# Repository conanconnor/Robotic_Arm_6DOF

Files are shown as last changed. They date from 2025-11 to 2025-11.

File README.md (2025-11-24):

# Robotic Arm 6-DOF

| **Christopher Abdul-Ahad** | **Conan Connor** |
|---|---|
| [GitHub](https://github.com/christopherabdulahad) · [LinkedIn](https://www.linkedin.com/in/christopherabdul-ahad/) | [GitHub](https://github.com/conanconnor) · [LinkedIn](https://www.linkedin.com/in/conanconnor/) |

A fully custom 6 degree of freedom robotic arm designed, built and programmed from scratch. This project was created as a personal engineering project to explore building a functional robotic system from the ground up.

https://github.com/user-attachments/assets/21fbbb61-f551-49d5-a1af-482c772e95da

<ins>**Goals**</ins>

The primary goal of this project was to design and build a fully functional custom 6-DOF pick-and-place robotic arm that could automate tasks similar to those found on assembly lines. As mechanical engineering students, we aimed to gain hands-on experience, implementing what we have learnt from theory - from initial CAD design to manufacturing, assembly and motion control programming. 

Our objectives included: 
- Understanding the complete robotics development process, from design to a fully operational product. 
- Designing a cost-effective, strong and reliable robotic arm, using 3D-printed components and commonly available hardware. 
- Developing motion control software in C++ using the Arduino IDE, achieving precise and predictable joint movements. 
- Creating a foundation for continuous improvement, allowing for future enhancements such as better actuators, sensors, and advanced control algorithms. 

This project was intended not only to produce a functional robotic manipulator but also to strengthen our capabilities in practical engineering design, prototyping and problem solving which are all key skills for any career in engineering. 

<ins>**Challenges**</ins>

Throughout the development process, we encountered several challenges, these include: 
- 3D printing tolerances: Very small holes and tight fit features designed in SolidWorks did not print accurately due to printer tolerances. 
- Support structure impact: Parts that required a lot of supports experienced surface imperfections or dimensional inaccuracies, affecting the assembly and motion smoothness. 
- Gravity and print orientation: Some components sagged during printing due to poor orientation or insufficient support. 
- Friction and mechanical losses: The gear system in the hand experienced higher friction than expected, reducing efficiency and motion smoothness. 
- Assembly complexity: Some components were difficult to fit together because accessibility was not fully considered during design. 

These challenges gave us valuable insight into Design for Manufacturing, specifically for additive manufacturing and low-cost robotics. 

<ins>**Solutions and Results**</ins>

To address these issues, we applied these solutions: 
- Drilling:  We used a hand drill to enlarge holes that printed undersized or not at all. 
- Sanding:  We sanded mating surfaces to improve fit and sliding motion. 
- Iterative redesign: Updated CAD models to correct structural or functional issues identified during testing. 

<ins>**Future Improvements**</ins>

If we were to continue developing this project or rebuild it from scratch we would add the following improvements: 
- Increase hole diameters in CAD to account for 3D-printing tolerances and avoid designing holes smaller than ~1 mm. 
- Optimise part geometry to reduce or eliminate the need for complex support structures. 
- Redesign print orientations to prevent sagging and ensure critical surfaces are printed cleanly. 
- Improve assembly by adding better access to screw holes 
- Refine the hand by redesigning gears to reduce friction and improve durability. 
- Upgrade control hardware in the future such as better servos, encoders or stepper motors for greater accuracy and load capacity. 




https://github.com/user-attachments/assets/dea5969e-bc63-4acd-a8a1-89a3208a30c9

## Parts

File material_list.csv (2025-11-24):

Catagory | Item | Quanitity
3D printed parts | All printed components | 24
Mechanical | M3 12mm countersunk screw | 18
Mechanical | M3 16mm countersunk screw | 7
Mechanical | M1 6mm screw | 6
Mechanical | M1.7 8mm screw | 16
Mechanical | M3 hexagon self-locking nylon nuts | 7
Electrical | Arduino UNO R3 | 1
Electrical | 5V 10A Power Supply | 1
Electrical | MG996R Servo Motor | 3
Electrical | SG90 Servo Motor | 3
Electrical | 30cm servo motor wire extender | 2
Electrical | 10cm servo motor wire extender | 1
Electrical | Male to male jumper wires | 4
Electrical | Female to male jumper wires | 15
Electrical | 16 AWG Wire | 1
Electrical | 10A Choc Block | 2

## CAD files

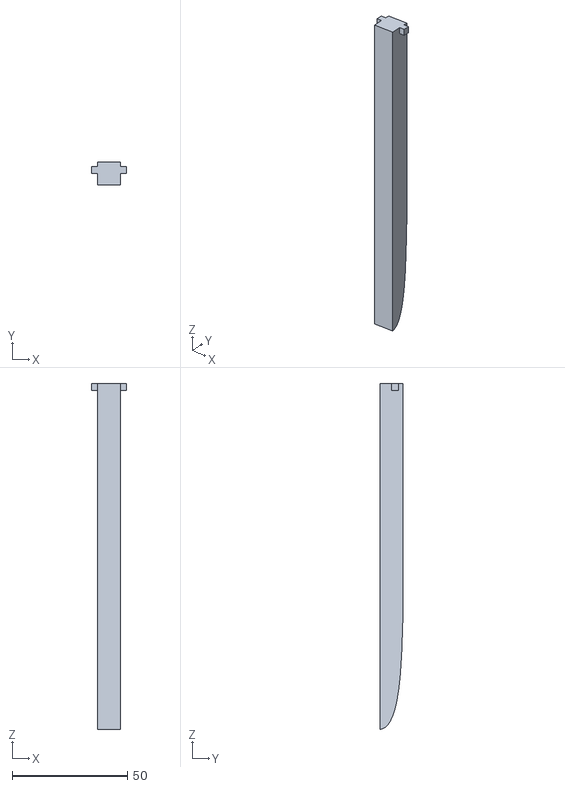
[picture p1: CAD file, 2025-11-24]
CAD/Leg_x6_BLUE.STL
15.0 x 10.0 x 150.0

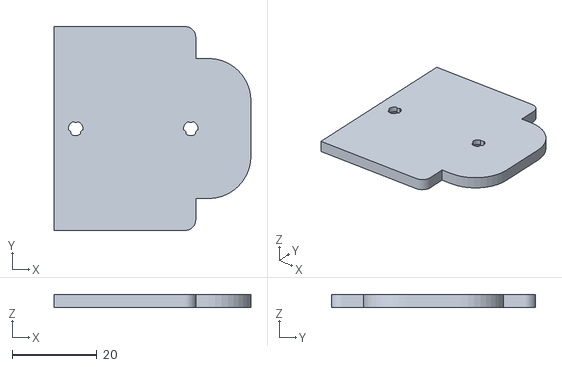
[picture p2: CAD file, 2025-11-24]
CAD/Hand_Base_Lid_BLUE.STL
46.4 x 48.0 x 3.00

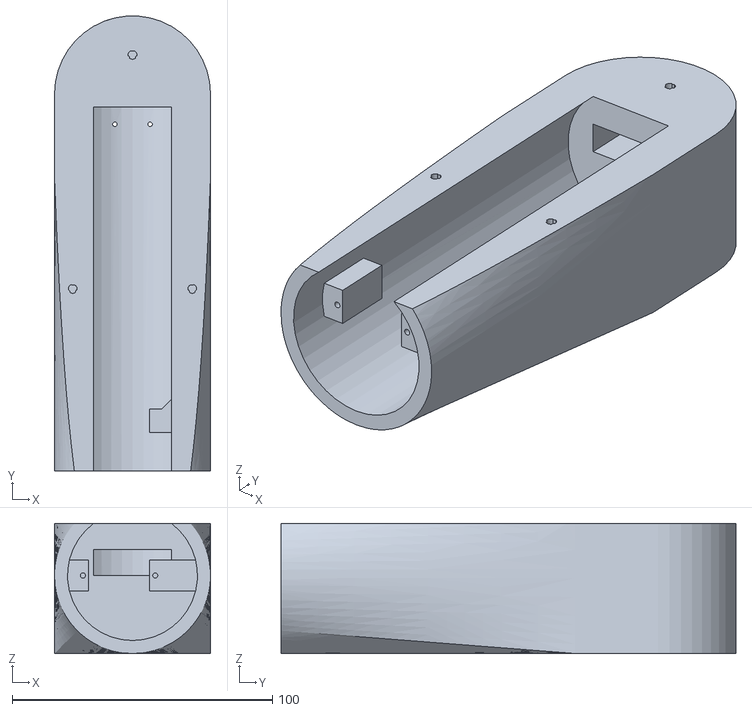
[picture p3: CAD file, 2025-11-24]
CAD/Forearm_BLUE.STL
60.0 x 174.9 x 50.0

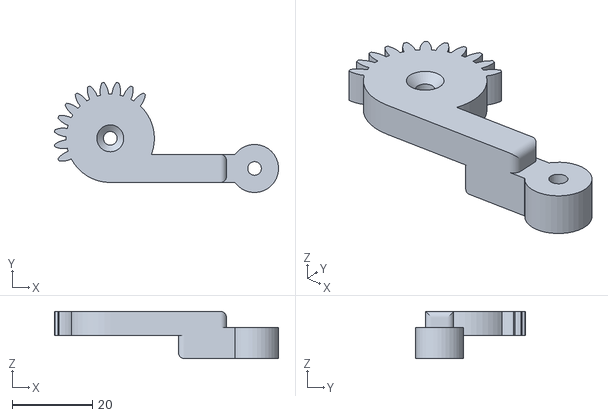
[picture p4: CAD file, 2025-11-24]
CAD/Hand_Mid_Otherside_WHITE.STL
55.9 x 27.4 x 11.8

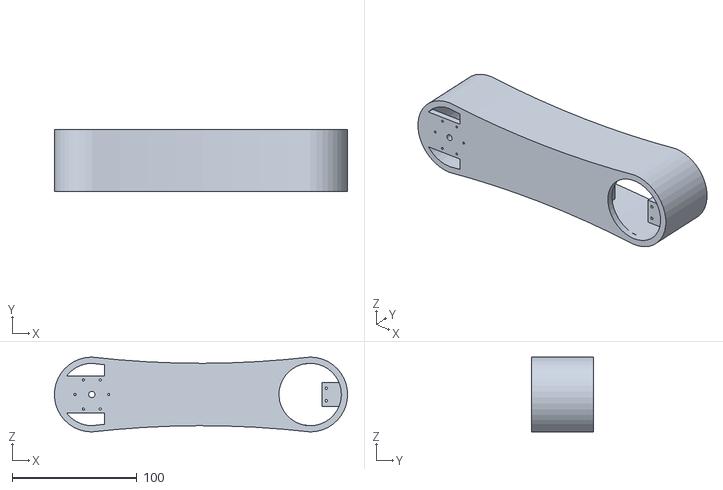
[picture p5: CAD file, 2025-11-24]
CAD/Upperarm_WHITE.STL
234.8 x 50.0 x 60.0

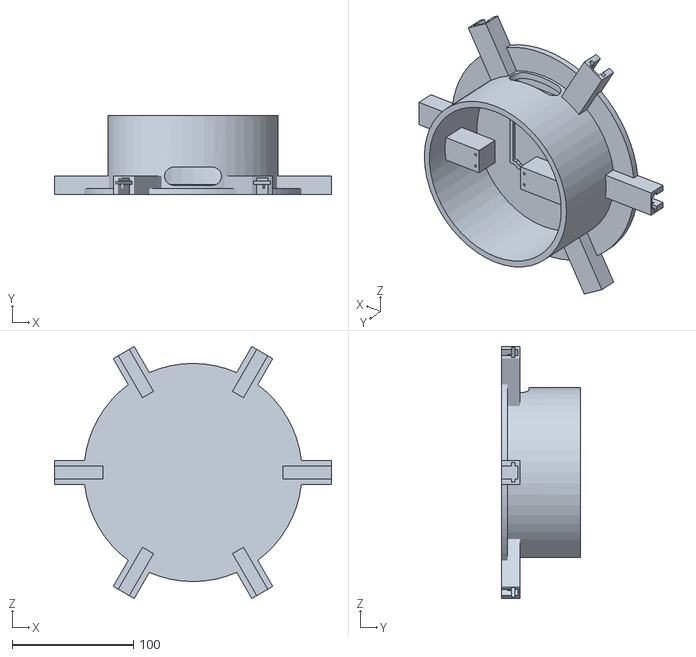
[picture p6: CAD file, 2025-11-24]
CAD/Base_WHITE.STL
228.6 x 65.0 x 207.9

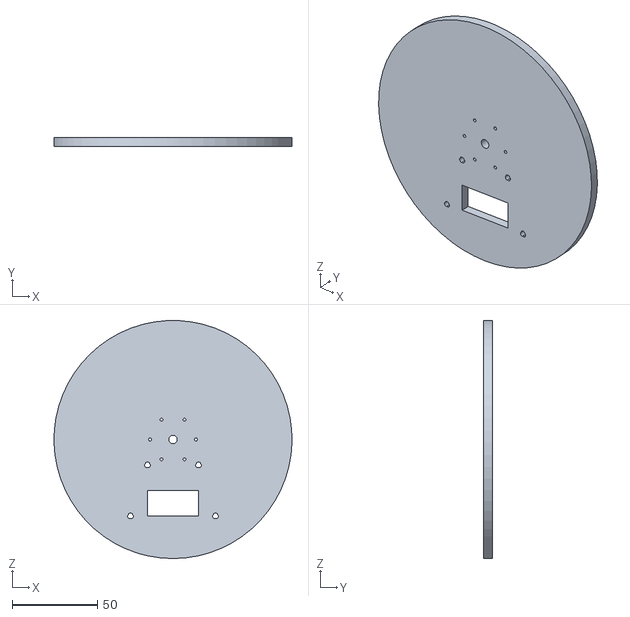
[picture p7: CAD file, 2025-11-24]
CAD/Base_Lid_BLUE.STL
140.0 x 5.00 x 140.0

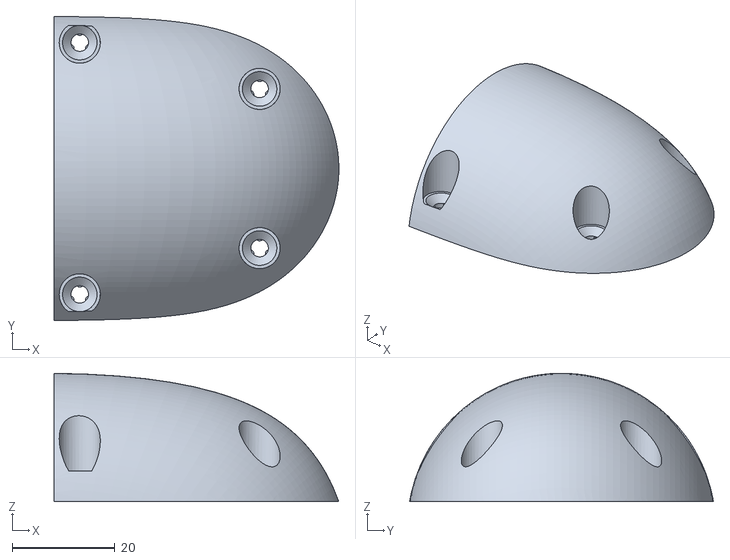
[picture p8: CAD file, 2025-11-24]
CAD/Wrist_Lid_WHITE.STL
55.4 x 59.2 x 25.0

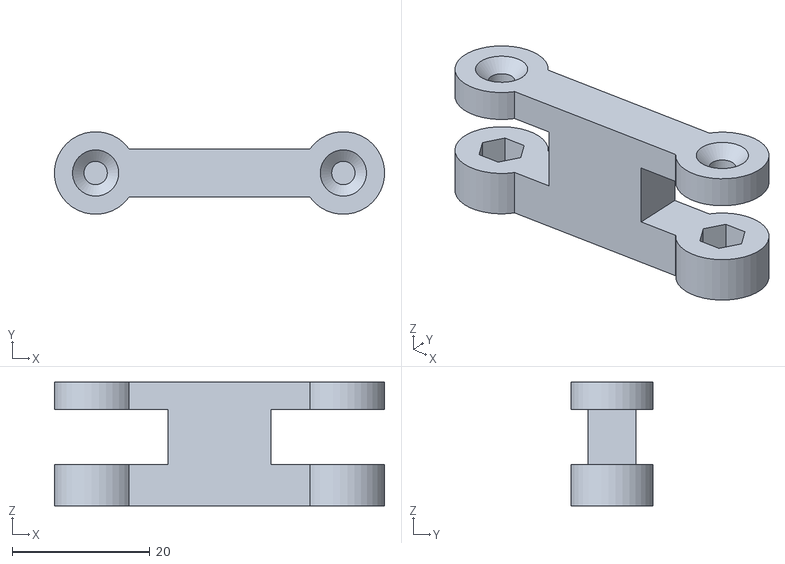
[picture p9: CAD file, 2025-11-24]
CAD/Hand_Small_x2_WHITE.STL
48.0 x 12.0 x 18.0

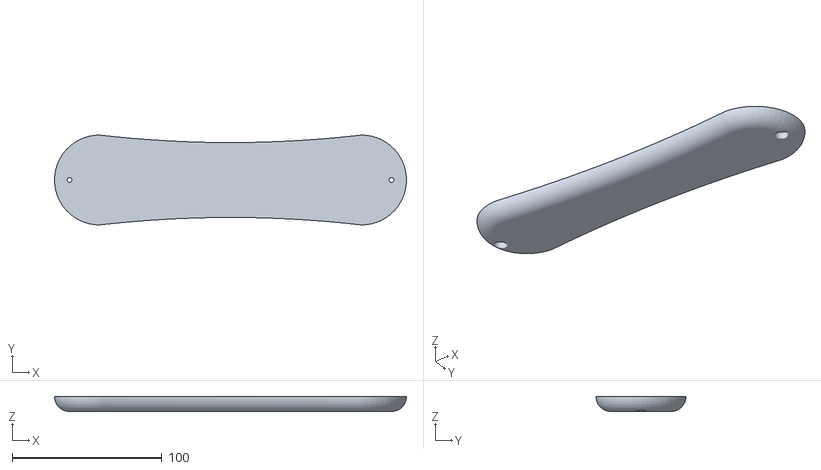
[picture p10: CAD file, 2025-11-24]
CAD/Upperarm_Lid_WHITE.STL
235.0 x 60.0 x 10.00

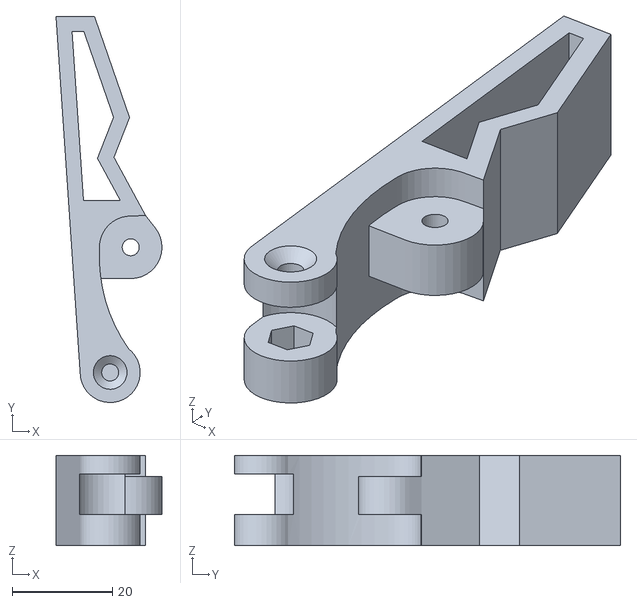
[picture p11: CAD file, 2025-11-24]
CAD/Hand_Big_BLUE.STL
21.2 x 77.1 x 18.0

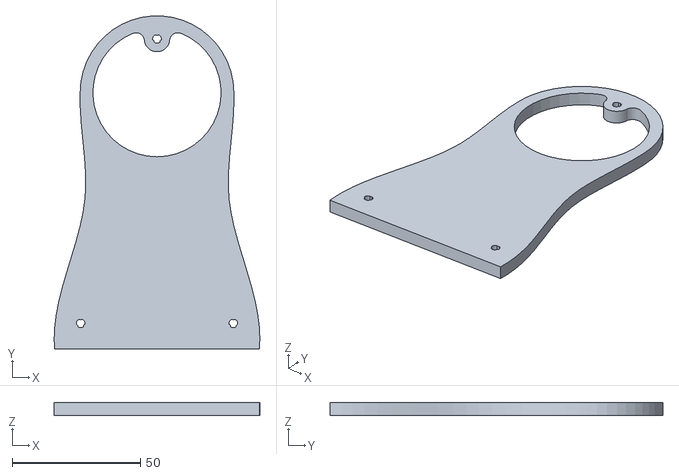
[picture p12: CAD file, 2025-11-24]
CAD/Sholder_Lid_BLUE.STL
80.3 x 129.9 x 5.00

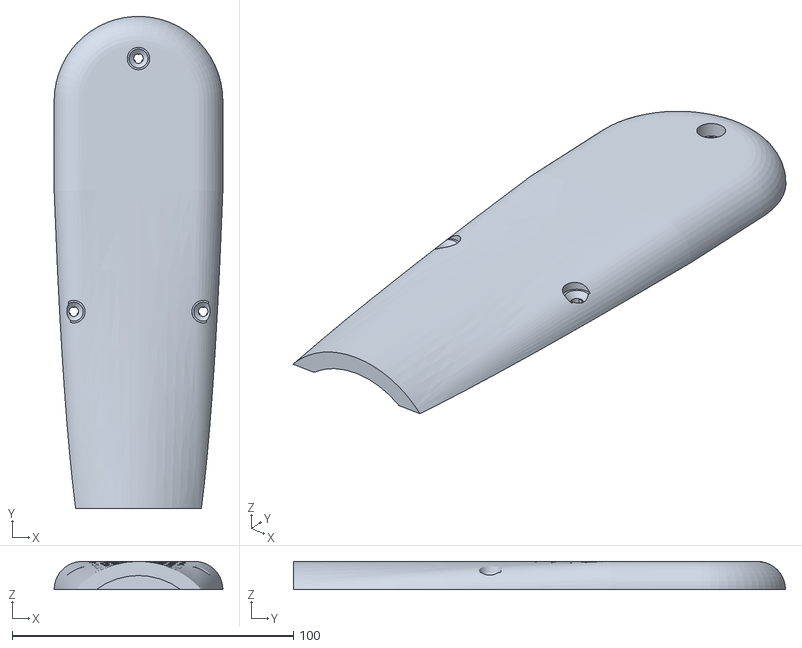
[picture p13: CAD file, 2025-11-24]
CAD/Forearm_Lid_BLUE.STL
60.0 x 175.0 x 10.00

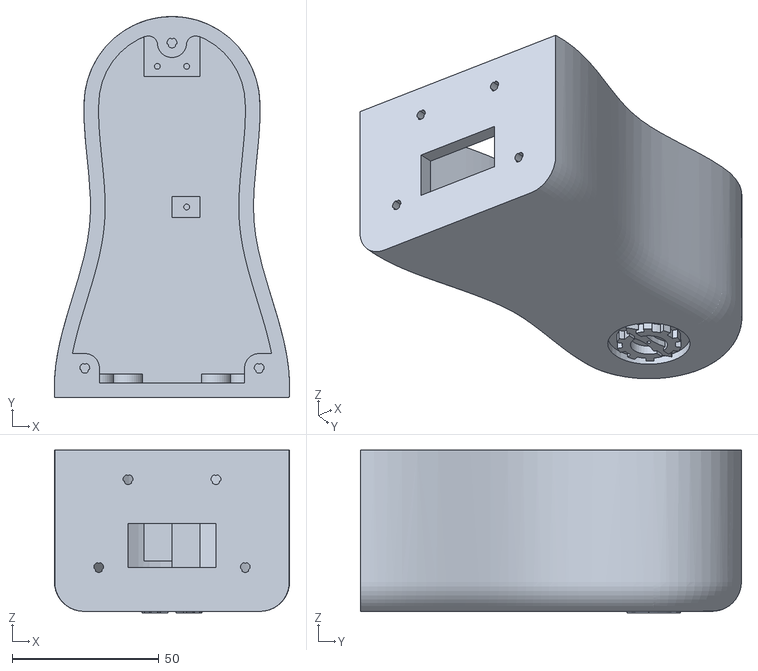
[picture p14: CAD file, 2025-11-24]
CAD/Sholder_BLUE.STL
80.3 x 130.0 x 55.5

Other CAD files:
CAD/Hand_Big_Otherside_BLUE.STL
CAD/Hand_Base_BLUE.STL
CAD/Hand_Mid_WHITE.STL
CAD/Wrist_WHITE.STL

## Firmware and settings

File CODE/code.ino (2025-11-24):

#include <Servo.h>

const int num_joint = 6;

Servo joints[num_joint];
int servoPins[num_joint] = {10, 9, 11, 12, 8, 13};
int currentAngles[num_joint] = {115, 90, 155, 90, 90, 110};

String jointNames[num_joint] = {
  "BASE", "SHOULDER", "ELBOW", "FOREARM", "WRIST", "HAND"
};

void setup() {
  Serial.begin(9600);

  for (int i = 0; i < num_joint; i++) {
    joints[i].attach(servoPins[i]);
    joints[i].write(currentAngles[i]);
  }

  Serial.println("Arm online...");
  Serial.println("Use: <JOINT> <ANGLE> <MS_PER_DEG>");
}

void loop() {
  if (Serial.available()) {
    String cmd = Serial.readStringUntil('\n');
    cmd.trim();
    if (cmd.length()) handleCommand(cmd);
  }
}

void moveServo(int joint, int targetAngle, int stepDelay) {
  targetAngle = constrain(targetAngle, 0, 180);

  int current = currentAngles[joint];
  int step = (targetAngle > current) ? 1 : -1;

  for (int pos = current; pos != targetAngle; pos += step) {
    joints[joint].write(pos);
    delay(stepDelay);
  }

  joints[joint].write(targetAngle);
  currentAngles[joint] = targetAngle;
}

void handleCommand(String cmd) {
  int s1 = cmd.indexOf(' ');
  int s2 = cmd.indexOf(' ', s1 + 1);

  if (s1 < 0 || s2 < 0) {
    Serial.println("You sure that command works?");
    return;
  }

  String jointName = cmd.substring(0, s1);
  int angle = cmd.substring(s1 + 1, s2).toInt();
  int speed = cmd.substring(s2 + 1).toInt();

  int idx = -1;
  for (int i = 0; i < num_joint; i++) {
    if (jointNames[i].equalsIgnoreCase(jointName)) {
      idx = i;
      break;
    }
  }

  if (idx == -1) {
    Serial.println("Hmm... can't find that joint.");
    return;
  }

  if (speed < 1) speed = 1;

  moveServo(idx, angle, speed);

  Serial.print(jointNames[idx]);
  Serial.print(": ");
  Serial.print(angle);
  Serial.print(" (");
  Serial.print(speed);
  Serial.println(" ms/deg)");
}

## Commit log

2025-11-24 Added CAD
2025-11-24 Create CAD
